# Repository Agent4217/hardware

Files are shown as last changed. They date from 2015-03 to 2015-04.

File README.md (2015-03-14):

# hardware
The repo for BBP hardware.

Licence: CC-BY-SA
http://creativecommons.org/licenses/by-sa/4.0/

Features:
Microcontroller
-	Texas Instrument Sitara AM335x, 1GHZ Cortex-A8 ARM
-	2 Programmable Realtime Units (PRU) to generate really high frequency step and dir signals
-	4GB eMMC
-	512M DDR3 memory
-	10/100M ethernet
-	microSD card
-	USB Host to connect USB disk, WiFi, Camera .etc
-	USB Device interface, shows to the computer as a mass storage device
Stepper drivers
-	5 to 6 DRV8825 stepper drivers
-	1/32 microsteps per step
-	Each capable of driving bipolar steppers up to 45V and 2.5A
-	Digital control of the current setting for each driver
Outputs
-	3 heaters, 2 for extruder and 1 for HBP
-	6 connectors for fan or LED light belt, all adjustable
Inputs
-	3 Thermistor (ADC) inputs
-	2 Thermalcouple (MAX6675) inputs
-	6 endstops
-	1 connector for external power button
Extensibility
-	50 pins FFC connector for 24 bits TFT LCD and touch screen
-	connector for 2 extended steppers
-	connector for 3 extended heaters
-	Serial connector to print debug log
-	Lots of pins broken out, including step, direction and enable pins for the stepper drivers

Inspired by the priors who have done a lot of great jobs before.

BeagleBone Black
Author: Beagleboard.org
http://beagleboard.org/

replicape
Author: Elias Bakken
http://www.thing-printer.com/

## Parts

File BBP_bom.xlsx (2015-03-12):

Part | Reference | PCB Footprint | Quantity | Price
FPC50PIN | CN1 | FPC50PIN-0_5H2A | 1
KF2EG 5.08-4P | POWER | KF2EG 5.08-4P | 1
KF128-5.08-2p | H_EXT1,H_EXT2,H_HBP | KF128-5.08-2p | 4
HDR2 | Z1,Y1,X1,J1,Z2,Y2,X2,J14,J15,J16,J17,J18 | HDR1X2_2.54 | 12
HDR4 | J19,J20,J21,J22,J23 | HDR1X4_2.54 | 6
HDR3 | T_EXT1,T_EXT2,T_HBP,J2 | HDR1X3_2.54 | 4
CON2 | J24 | 2.54 | 1
USB-AM-SMD | USB1 | USB-AM-DIP | 1
USB-MICRO | USB2 | USB-MICRO | 1
LPJ0011BBNL | P2 | RJ45-7499010211A | 1
SCHA5B0200 | P3 | SD-MICRO-SCHA5B0300 | 1
KMR231GLFS | S1,S2 | TVCM16 | 2
LED0603 Blue | D1,D2,D3,D4,D6 | LED0603 | 5
LED0603 Green | D7,D8,D11,D12,D15 | LED0603 | 5
MBRA340T3 | D9,D10,D13,D16,D17,D18,D19 | DO-214-SS34 | 7
0.1 Ohm,0805 | FB1 | L0805 | 1
150OHM800mA | FB2,FB3,FB4,FB5,FB6 | L0805 | 5
LQM2HPN2R2MG0L | L1,L2,L3 | L2520 | 3
33UH | L6 | L-SMD-8 | 1
4.7uH | L7 | L-SMD-5.6
2.2uH-DCR<0.1R-1.5A | L8 | L4018 | 1
NIF5002 | Q1,Q3,Q5,Q8,Q9 | SOT-223 | 5
AON6758 | Q2,Q4,Q6 | DFN5X6 | 3
AO3423 | Q7 | SOT-23 | 1
TPS65217C | U1 | U_48_RSL | 1
SY8009C | U2 | SOT23-5 | 1
SN74LVC1G07DCK | U3 | DCK5_2P15X1P4 | 1
XAM3359AZCZ100 | U4 | am33xx_15x15 | 1
SN74LVC1G06DCK | U5 | DCK5_2P15X1P4 | 1
SN74LVC2G241 | U6 | DCK5_2P15X1P4 | 1
RCLAMP0524P/NC | U7,U9 | RCLAMP0524P | 2
TPS2051 (DGN) | U8 | DGN-16X60 | 1
MT41K256M16HA -125:E | U10 | BGA96_T9_P8_9X14 | 1
MTFC2GMVEA-0M WT | U11 | BGA153_P14_P5_11P5X13 | 1
LAN8710A | U12 | QFN32_5X5MM_EP3P3MM | 1
CAT24C256 | U13 | msop8 | 1
MCP1402 | U16,U18,U20 | SOT23-5 | 3
RT8268 | U17 | MSOP10 | 1
MCP16321 | U19 | QFN16 | 1
DRV8825PWP | U21,U24,U25,U28,U29 | HTSSOP28 | 5
DAC088S085 | U22 | MSOP16 | 1
SN74AHC595PW | U23,U26,U27,U30,U31 | MSOP16 | 5
32.768KHz MC-306 | X3 | XTAL4_126-216SMD | 1
24MHz | X4 | XTAL150SMD_125X196 | 1
25.000MHz | Y3 | XTAL150SMD_125X196 | 1
10uF,10V | C1,C2,C4,C5,C6,C7,C8,C9,C10,C11,C12,C13,C37,C38,C53,C60,C75,C93,C94,C116,C120,C126,C137,C159 | C0805 | 24
0.1uf,6.3V | C3,C24,C25,C28,C30,C31,C33,C34,C35,C36,C39,C40,C41,C42,C43,C44,C45,C46,C47,C48,C49,C50,C51,C52,C54,C55,C56,C57,C58,C59,C61,C62,C63,C64,C65,C66,C67,C68,C69,C70,C71,C72,C73,C74,C76,C77,C78,C79,C80,C81,C82,C83,C84,C85,C86,C90,C91,C92,C95,C96,C97,C98,C99,C100,C101,C103,C105,C106,C107,C108,C109,C110,C111,C112,C113,C114,C115,C117,C118,C119,C122,C124,C125,C128,C138,C139,C140,C141,C158,C160,C193 | C0402 | 91
2.2uF,6.3V | C14,C16,C123 | C0402 | 3
4.7uF | L7,C15 | C0603 | 2
0.1uF | C18,C190,C192,C199,C202,C204,C205,C212,C214,C216,C217 | C0402 | 11
18pF,50V | C19,C21,C22,C23 | C0402 | 4
2.2uF,10V | C20 | C0402 | 1
0.001uf,50V | C29 | C0402 | 1
100uF,6.3V | C32 | SMD3MM | 1
1uF,10V | C87,C88,C89,C102,C104,C127 | C0402 | 6
0.001uf,6.3V | C121 | C0402 | 1
470pF,6.3V | C129 | C0402 | 1
15pF,NC | C130,C131,C132,C133 | C0402 | 4
0.022uF,10V | C134 | C0402 | 1
30pF,50V | C135,C136 | C0402 | 2
0.47uF | C161,C162,C163,C164,C165,C166 | C0603 | 6
100uF/25V | C167 | SMD3MM | 1
4.7uF/16V | C168,C176,C184 | C0805 | 3
0.1uF/16V | C169,C177,C185 | C0603 | 3
4.7nF/25V | C170,C178,C186 | C0402 | 3
10nF | C171,C174,C187,C194,C196,C206,C208 | C0402 | 7
10uF,25V | C172 | C0805 | 1
22uF/25V | C173 | C1206 | 1
1nF | C175 | C0402 | 1
22nF | C179 | C0402 | 1
10uF/25V | C180,C181 | C0805 | 2
22uF | C182,C183 | C0805 | 2
0.1uF/25V | C188,C189,C195,C197,C198,C200,C207,C209,C210,C211 | C0603 | 10
4.7uF/25V | C191,C201,C203,C213,C215 | C0805 | 5
10uF | C218 | C0805 | 1
1.5K,1% | R1,R2,R42,R57,R58,R59,R64 | R0402 | 7
100K,1% | R3,R29,R92,R93,R94,R95,R96,R97,R98,R99,R100,R101,R102,R174,R181,R182,R183,R187 | R0402 | 18
0,1% | R4,R5,R6,R7,R13,R16,R27,R34,R35,R36,R82,R87 | R0402 | 12
0,NC | R8 | R0402 | 1
100K,1% | R9 | R0402 | 1
442K,1% | R10 | R0402 | 1
4.75K,5% | R11,R91 | R0402 | 2
10k,1% | R12,R39,R40,R41,R43,R45,R46,R47,R48,R49,R50,R51,R52,R53,R54,R55,R56,R60,R61,R62,R63,R80,R90,R106,R107,R108,R109,R110,R111,R112,R196 | R0402 | 31
1M,1% | R14 | R0402 | 1
10K | R15,R17,R18,R134 | R0402 | 4
10.8K,5% | R19 | R0402 | 1
49.9,1% | R20,R65,R66,R67,R68 | R0402 | 5
4.7K | R21,R22,R23,R125,R126,R127,R128,R129,R135,R136,R137,R138,R143,R144,R146,R148,R151,R152,R157,R158 | R0402 | 20
4.75K,1% | R24,R25,R26 | R0402 | 3
33 | R28 | R0402 | 1
22 | R30 | R0402 | 1
0 | R31,R32,R33 | R0402 | 3
0,1%,NC | R37 | R0402 | 1
0R,1%,NC | R38 | R0402 | 1
240R,1% | R44 | R0402 | 1
10,1%,NC | R69 | R0402 | 1
100,1% | R70,R71,R72,R73,R74,R76,R78,R79,R83,R84,R178 | R0402 | 11
470,5% | R75,R77 | R0402 | 2
.1, 1‰, | R81 | R0805 | 1
0,1%,NC | R85 | R0402 | 1
1M,1%,NC | R86 | R0402 | 1
10,1% | R88 | R0402 | 1
12.1K,1% | R89 | R0402 | 1
100K,1%,NC | R103,R104,R173,R175,R176,R177,R179,R180,R184,R185,R186,R188,R189,R190,R191,R192 | R0402 | 16
0R,NC | R105,R194 | R0402 | 2
1K | R113,R114,R115,R116,R117,R118 | R0402 | 6
4.7K,1% | R119,R120,R121 | R0402 | 3
6.8K | R122,R123,R124 | R0402 | 3
100R | R130,R139,R140,R147 | R0402 | 4
0R | R131,R163,R164,R165,R166,R167,R168,R169,R170,R171,R172 | R0402 | 11
120K | R132 | R0402 | 1
40K | R133 | R0402 | 1
30k,NC | R141 | R0402 | 1
100K | R142 | R0402 | 1
0.1R/0.1% | R149,R150,R153,R154,R155,R156,R159,R160,R161,R162 | R0805 | 10
100k,5% | R193 | R0402 | 1
36K,5% | R195 | R0402 | 1
10k,NC | R197 | R0402 | 1

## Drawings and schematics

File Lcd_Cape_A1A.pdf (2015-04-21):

## R17: R=300mV/I(led)

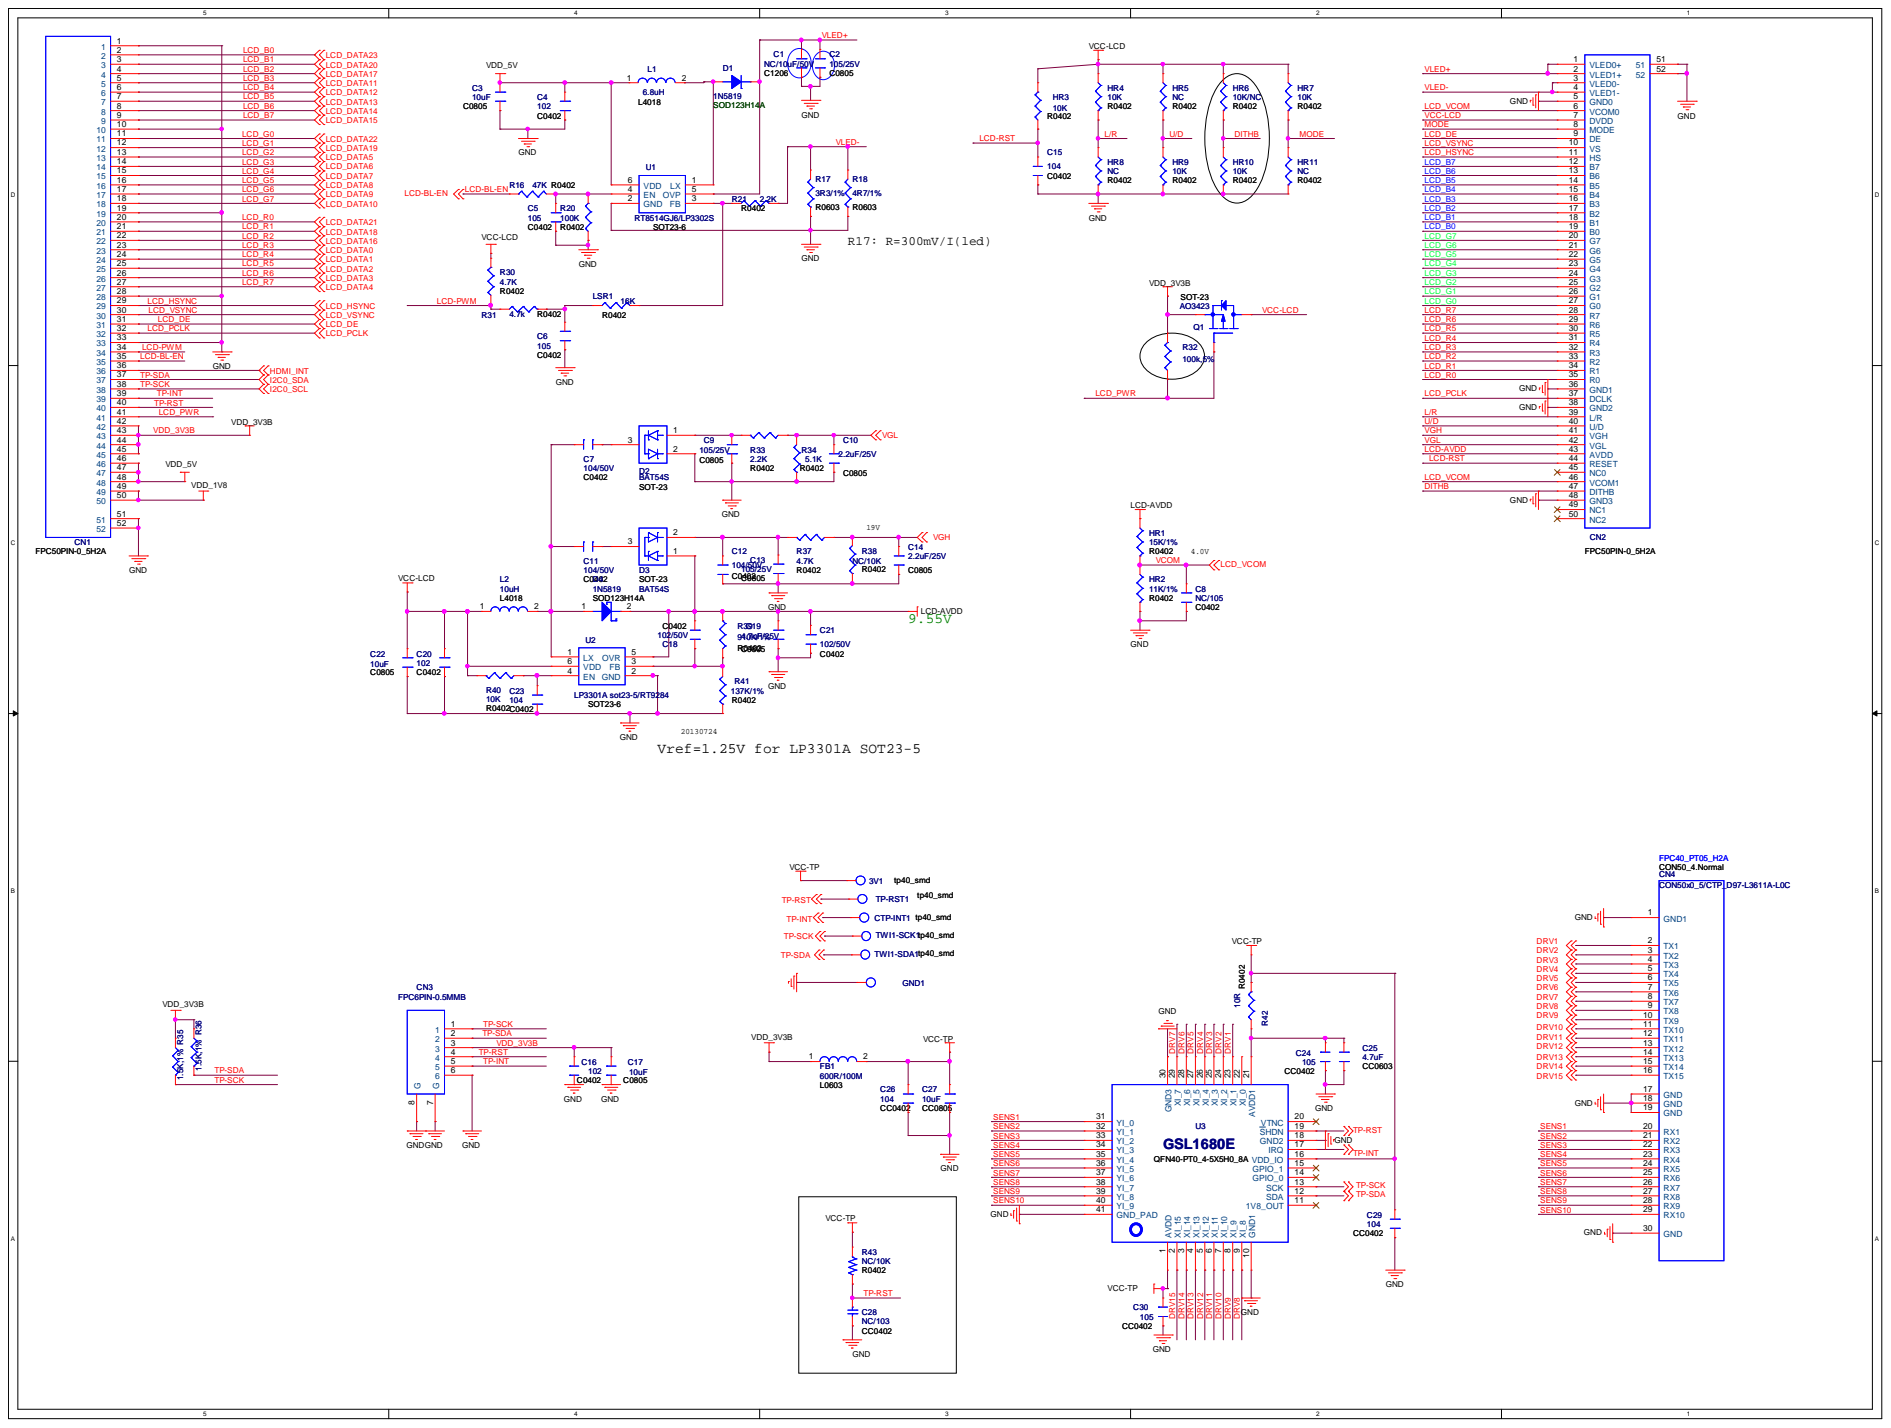
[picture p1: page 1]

## GREEN

## RED

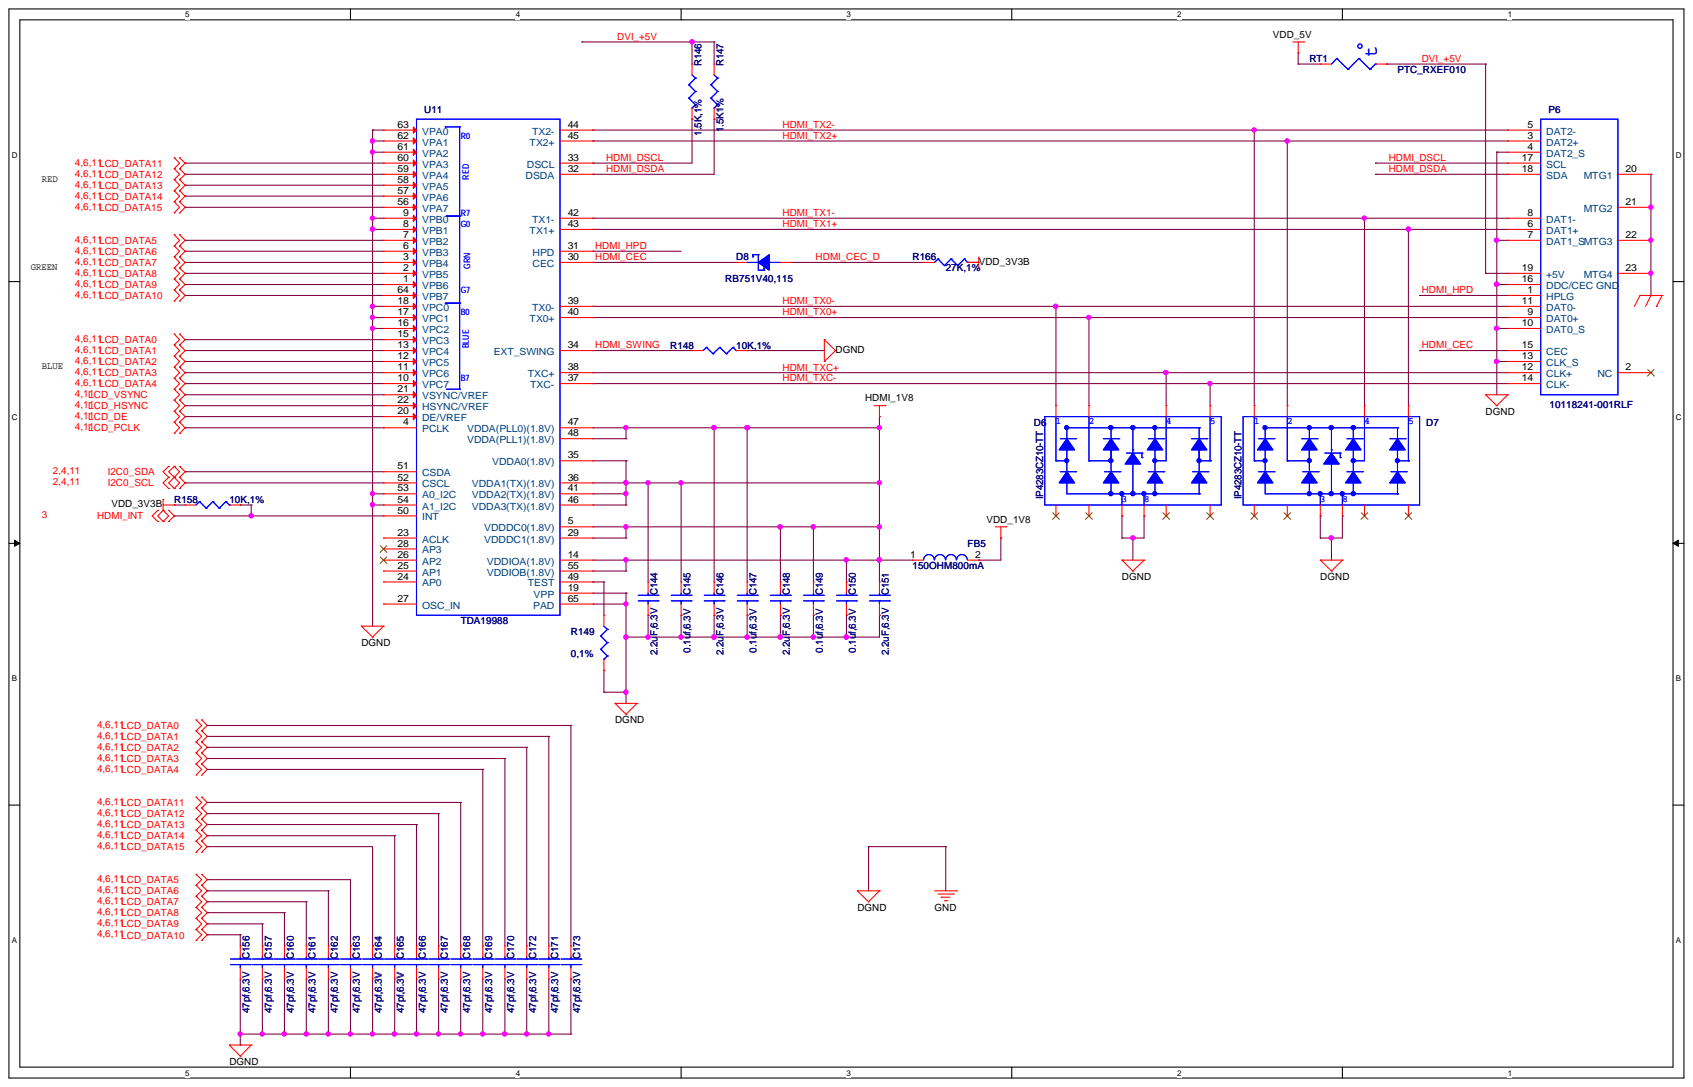
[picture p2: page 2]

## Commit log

2015-03-12 init repo
    [BBP_SCH.DSN, BBP_bom.xlsx]
2015-03-14 add BBP_Garber
    [NC.drl]
